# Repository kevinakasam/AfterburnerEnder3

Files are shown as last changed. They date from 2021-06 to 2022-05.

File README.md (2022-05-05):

## Afterburner Ender3 + Cable Chain + BL-Touch or PINDA + Raspberry Pi TFT

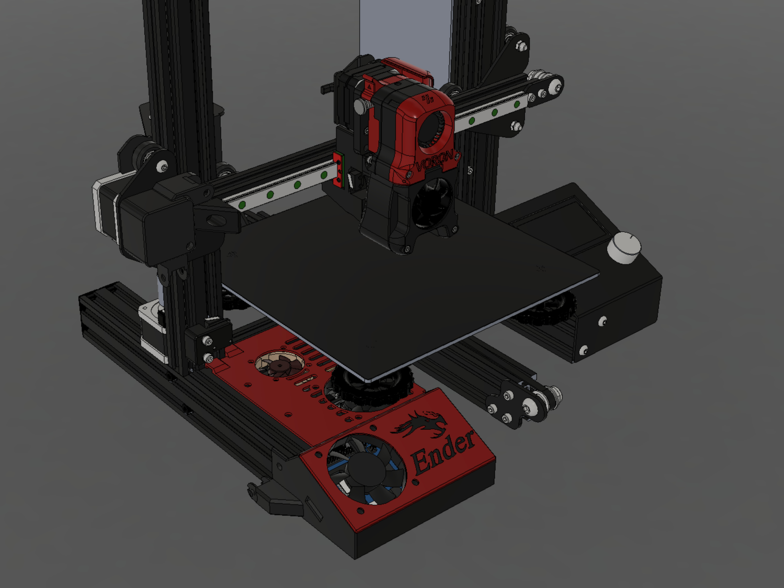
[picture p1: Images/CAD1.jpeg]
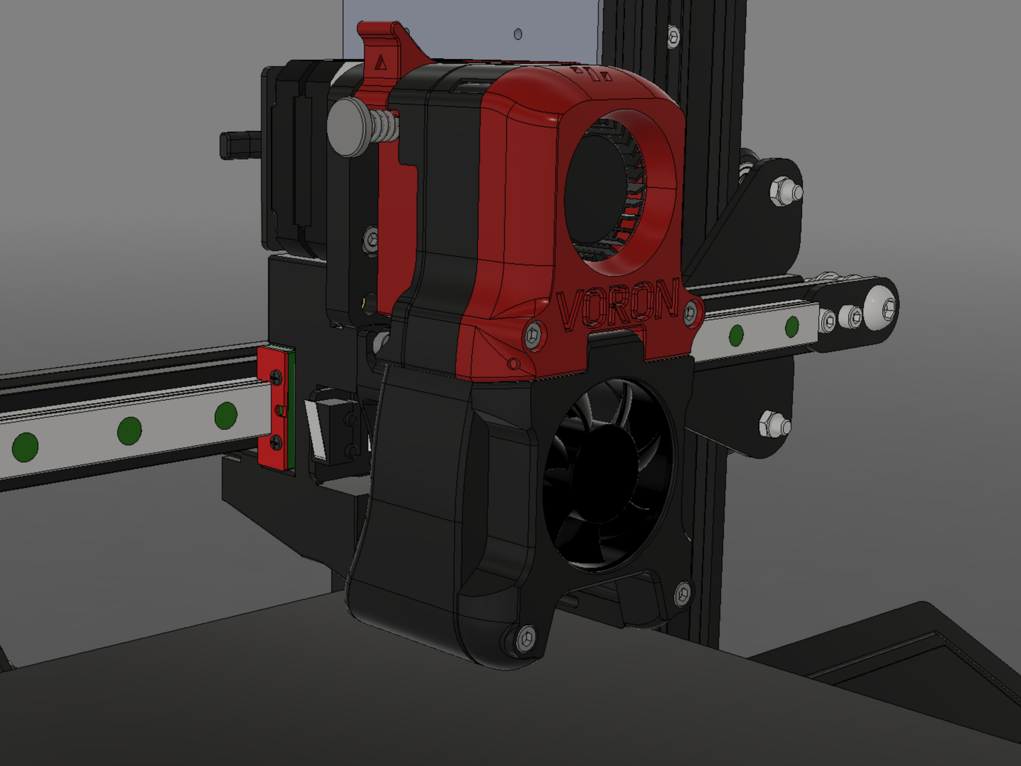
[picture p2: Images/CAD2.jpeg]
 
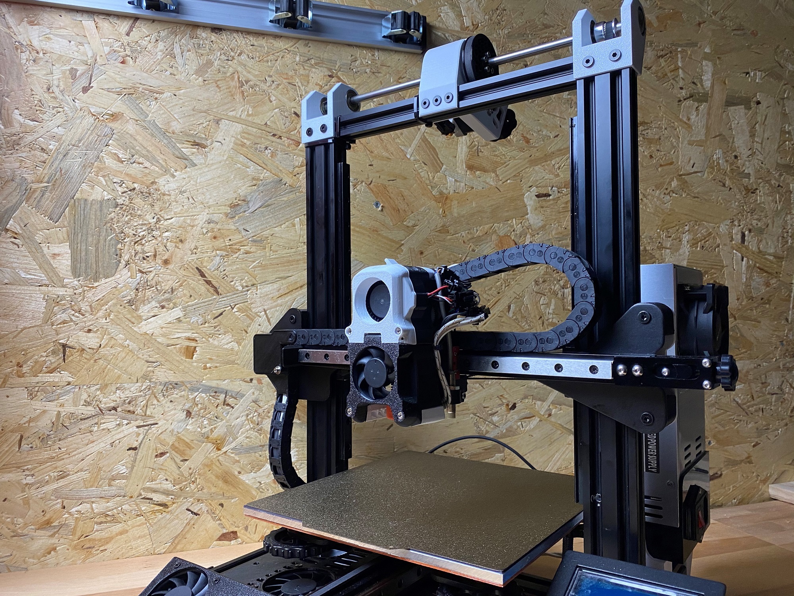
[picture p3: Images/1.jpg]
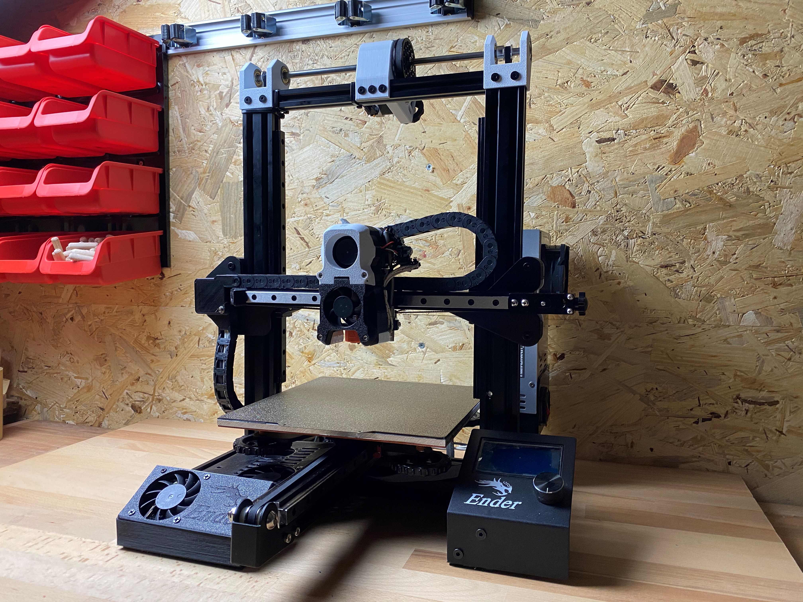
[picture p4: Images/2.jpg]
 

If you have any questions feel free to join the [Discord-Server](https://discord.gg/xqpKrxt9FC) 
 
<a href="https://discord.gg/xqpKrxt9FC">
         <img alt="Join" src="https://github.com/kevinakasam/BeltDrivenEnder3/blob/main/Pictures/Discord-Logo%2BWordmark-Color.png"
         width=250" >
      </a>

## Still in Progess
This page is currently only used to provide the files and basic instructions. More info and parts for the electronics, Raspi, BL-Touch etc will be added later.  

### Versions
1: PINDA or BL-Touch        |  2: Fan or Raspberry Pi TFT
:-------------------------:|:-------------------------:
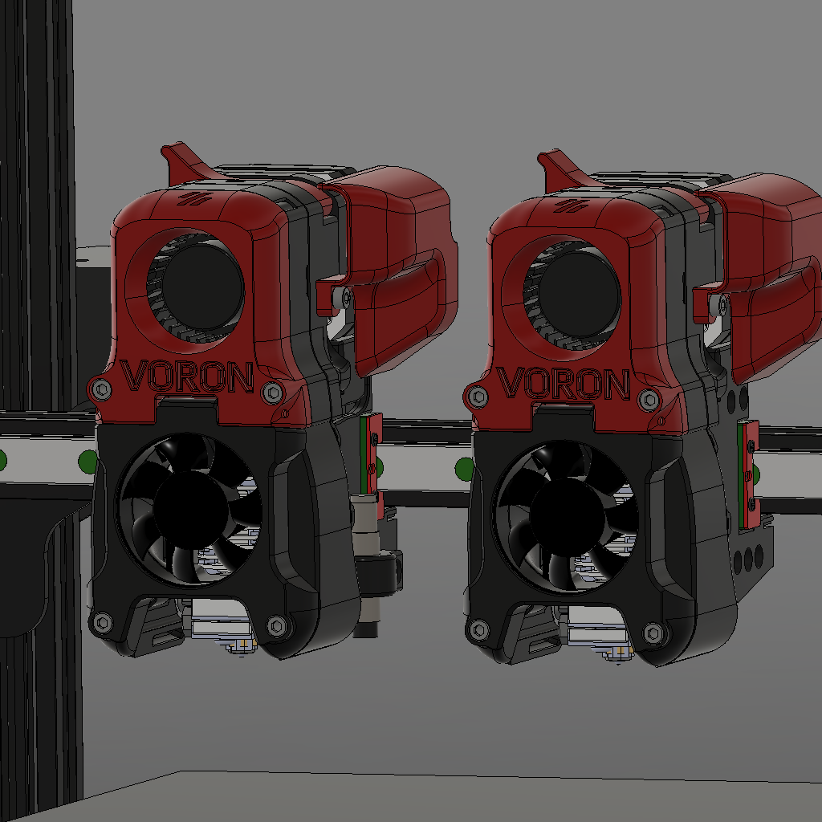
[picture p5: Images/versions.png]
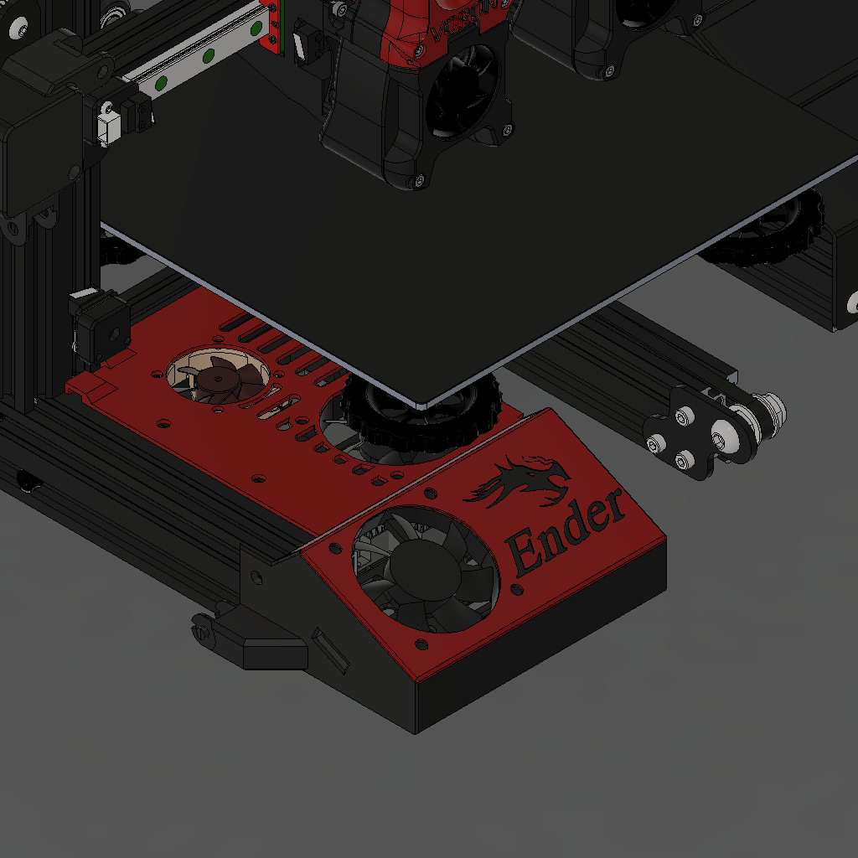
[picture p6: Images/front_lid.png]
  |  
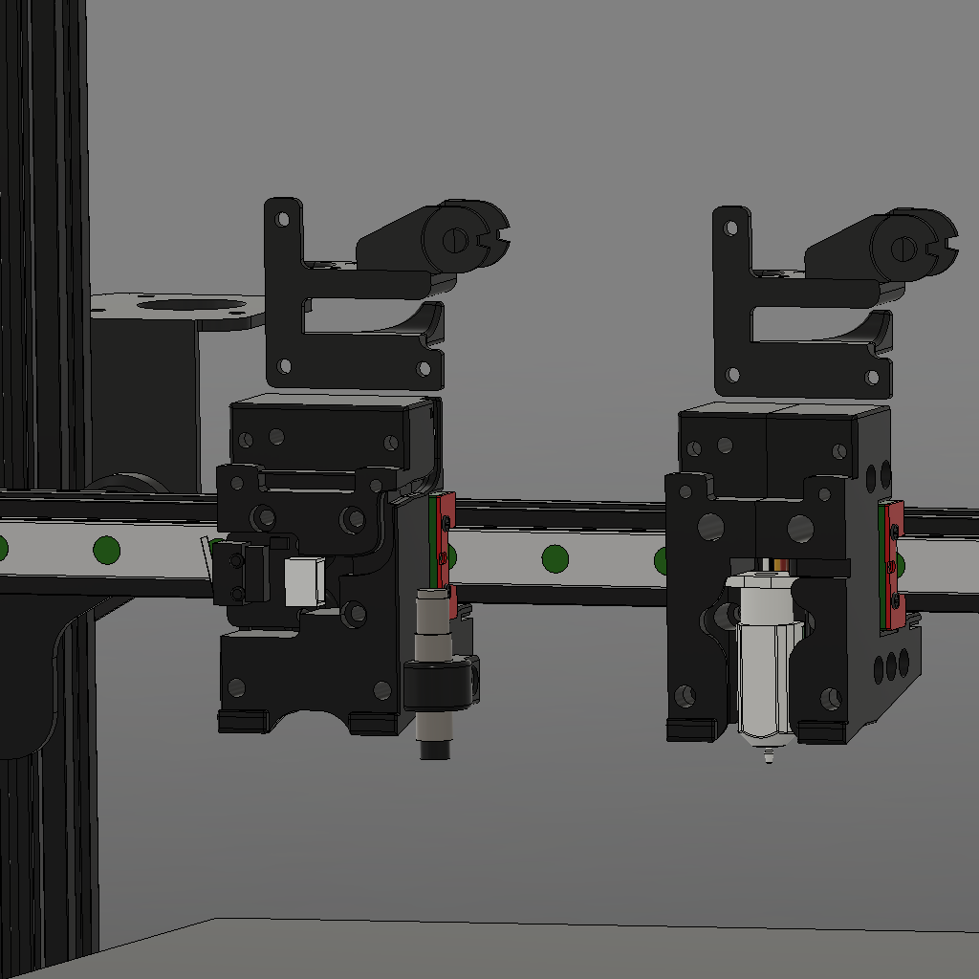
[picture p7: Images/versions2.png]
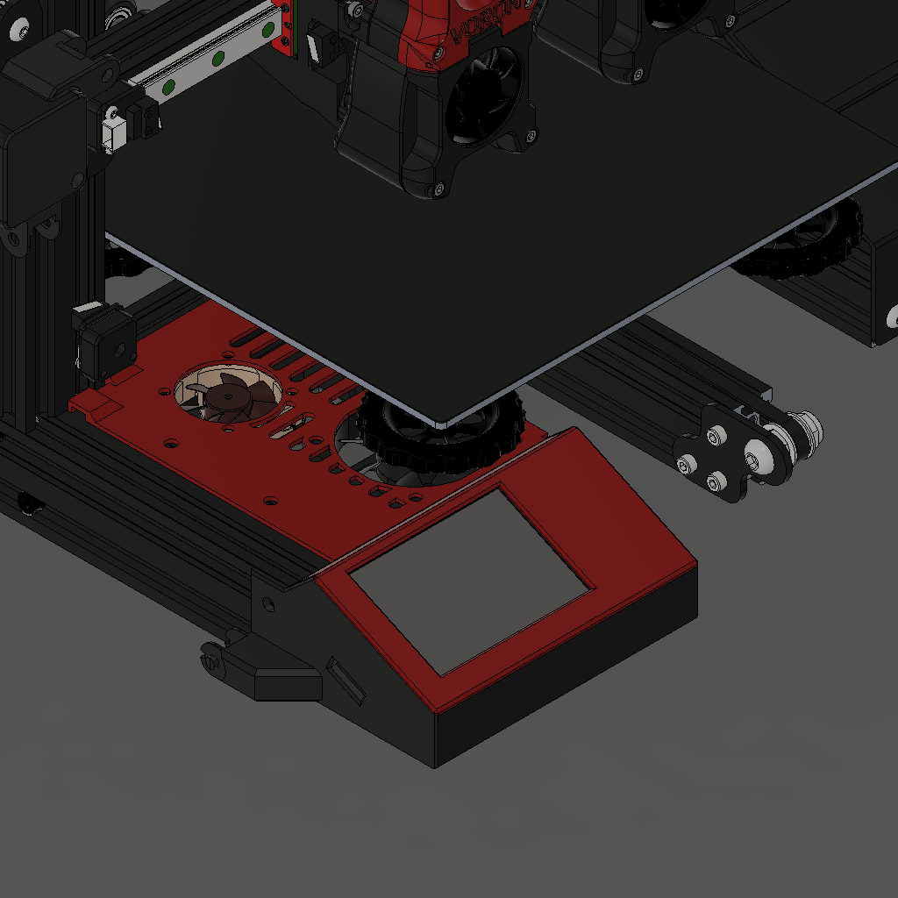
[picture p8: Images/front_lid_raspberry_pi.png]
  |  

### Why?
As you can probably guess, I love the Voron design. It makes me so much fun to work with the ideas and great designs that the team around Voron has created. And since the Afterburner not only looks nice but is also quite cheap and reliable, I decided to mount it on the Ender 3. This mod fits all Ender3 and similar machines like CR10 etc. Since the extruder had to come very far forward to be able to install the cable chain, I had a lot of space in the afterburner carriage. Therefore, I decided to integrate the limit switch into the carriage.

### A good Idea?
Definitely yes, if you can print with ABS(+). I first printed the parts out of PETG and I had a lot of problems. Besides that, the extruder is very strong like the normal BMG extruder and just works perfectly. I have been using the extruder continuously for weeks now and I am very happy with it.
If you are from Germany or the EU, please send me a message via Discord and I can print the parts for you.

### Important SAFTY notes
Do not use the original cables in the cable chain! Do not use PVC cables, these will break after some time! I replaced all my cables with silicone cables, so they do not break. You can also use PTFE cables or HELUKABEL, but this is much more expensive. If you are from Germany you can find cheap silicone cables in the online store from Conrad Electronik.

### How to print?
All parts can be printed without support (except x_motor_housing.stl; see STL Folder) and are already in the optimal orientation for printing. All Afterburner parts should be printed out of Abs. I'm using Esun ABS+, this is very easy tp print. But remember that the fumes are toxic, so use an enclosure and an air filter ([BFACH](https://github.com/kevinakasam/BFACH "BFACH")).

### BOM
* #### Rail
  * 1x MGN 12H 300mm
  * 12x M3x8mm (to mount the rail)
  * 12x M3 t-nut (to mount the rail)
  * 1x M5x8mm (to mount the limit block)
  * 1x M5 t-nut (to mount the limit block)
  * 2 Meter GT2 Belt (Glas Fiber reinforced)
* #### Afterburner Carriage Pinda
  * 3x M3x20mm
  * 1x M3x5mm
* #### Afterburner Carriage BL-Touch
  * 3x M3x20mm
  * 1x M3x5mm
  * 5x M3 brass heat insert
  * 5x M3x35mm
* #### PINDA Mout
  * 1x M3 brass heat insert
  * 1x M3x8mm
* #### BL-Touch Mount
  * 2x M3 brass heat insert
  * 2x M3x8mm
* #### Cable Chain
  * 1 Meter 10x11 cable chain (open and closed ine works. I used the open one for better access)
  * 3x M3 brass heat insert (for mounting to the chain anchor)
  * 3x M3x5mm (for mounting to the chain anchor)
* #### X Motor Housing
  * 3x M3x5mm (to mount the x-motor)
  * 1x M3x30mm (to mount the housing)
* #### Afterburner
  * Please use Voron sourcung guide: https://vorondesign.com/sourcing_guide (Click on the Afterburner sheet at the bottom)
  * **I'm using a 23mm nema. If you want to use a 20mm one you have to modify the parts!**
* #### Afterburner 5015 Mod
  * Please check Gregs page: https://github.com/Greg191134/Voron/tree/master/Afterburner%20Optimisation

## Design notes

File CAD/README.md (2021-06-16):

Feel free to edit the parts;)

 

Ender 3 CAD: https://github.com/Creality3DPrinting/Ender-3/tree/master/Ender-3%20Mechanical/F360

Afterburner CAD: https://github.com/VoronDesign/Voron-Afterburner/tree/master/CAD

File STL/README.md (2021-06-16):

### How to print?
All parts can be printed without support (except x_motor_housing.stl; see below) and are already in the optimal orientation for printing. All Afterburner parts should be printed out of Abs(+). I'm using Esun ABS(+), this is very easy tp print. But remember that the fumes are toxic, so use an enclosure and an air filter (spoiler: I'm going to release a very powerful fan soon). I added a small support structure to the afterburner_carraige.stl. just break it after printing (see red surface below).

I'm using Gregs Modulaar Fan Duct and 5015 Mod (https://github.com/Greg191134/Voron/tree/master/Afterburner%20Optimisation). I had a small gap between the extruder and tool part, so I moved the mounting holes 1mm up (see afterburner_carriage_5015mod.stl). Since I never tested the stock Afterburner, I don't know if this "error" also occurs with the normal Afterburner or only with Greg's mod. Feel free to give me feedback.

1: Add support to the upper chain mount        |  2: break the small bridge (red surface)
:-------------------------:|:-------------------------:
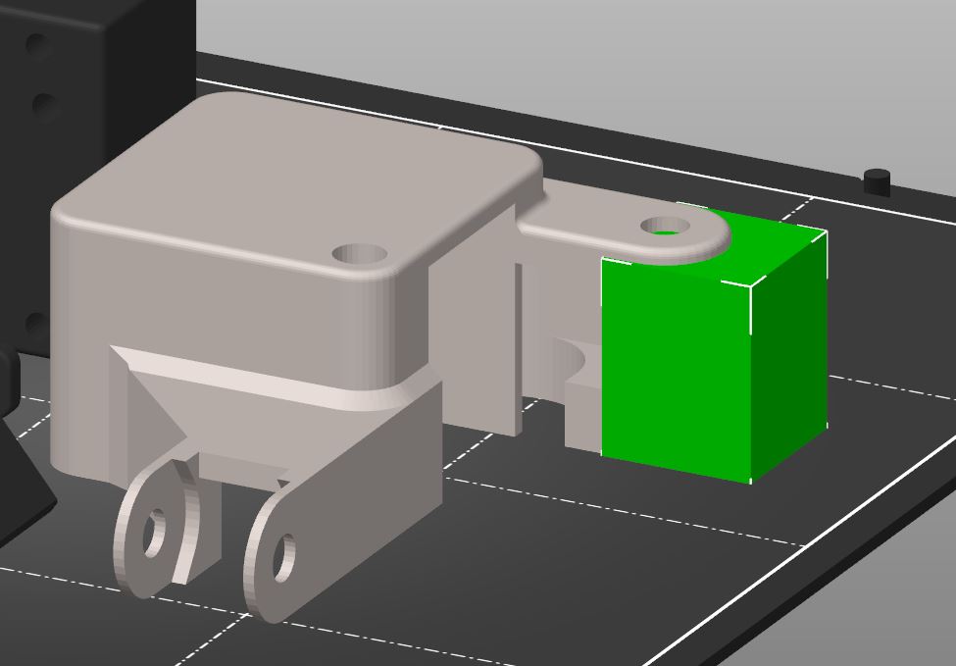
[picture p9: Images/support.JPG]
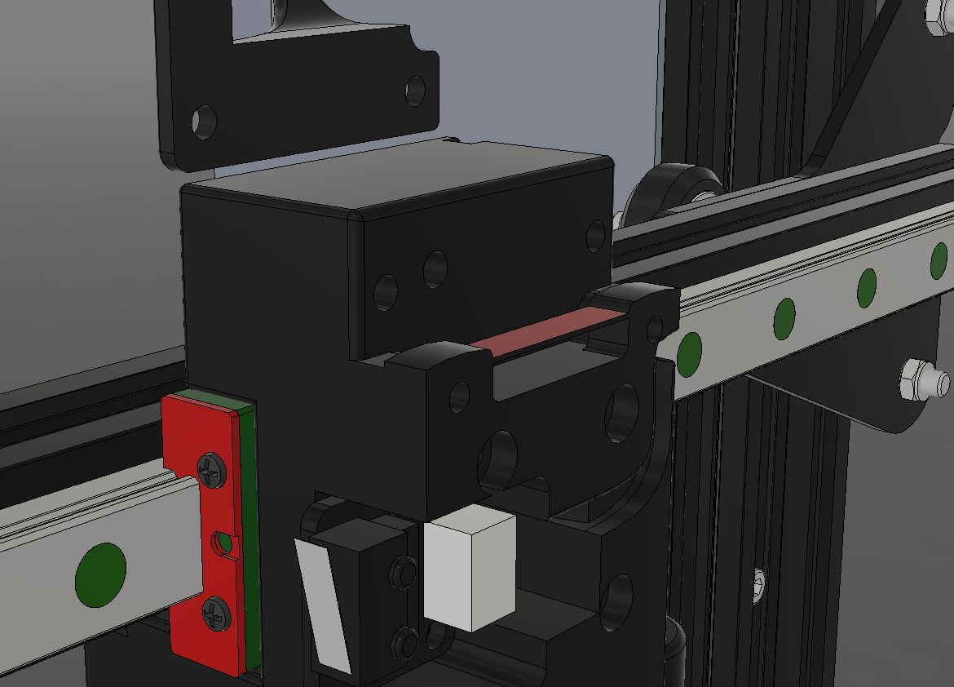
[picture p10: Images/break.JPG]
  |

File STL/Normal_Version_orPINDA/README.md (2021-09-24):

Carriage to mount the Afterburner to your Ender 3. Option to integrate the limit switch and add a PINDA. If you want to use a BL-Touch check the other version.

### How to print?
All parts can be printed without support and are already in the optimal orientation for printing.
I added a small support structure to the afterburner_carraige.stl (see red surface below). There's also some support in the end of the belt clamp. Just break both after printing.

I'm using Gregs Modulaar Fan Duct and 5015 Mod (https://github.com/Greg191134/Voron/tree/master/Afterburner%20Optimisation). I had a small gap between the extruder and tool part, so I moved the mounting holes 1mm up (see afterburner_carriage_5015mod.stl). Since I never tested the stock Afterburner, I don't know if this "error" also occurs with the normal Afterburner or only with Greg's mod. Feel free to give me feedback.



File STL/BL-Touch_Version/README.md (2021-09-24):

Mount that integrates the BL-Touch like the original Omron TL-Q5MC2. Very clean solution. All credits go to Guffy who came up with the idea and finished the design!

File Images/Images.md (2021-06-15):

Images.

Also check:

Video Tutorial (https://www.youtube.com/watch?v=bxTwFCPEIgg&t=1s)

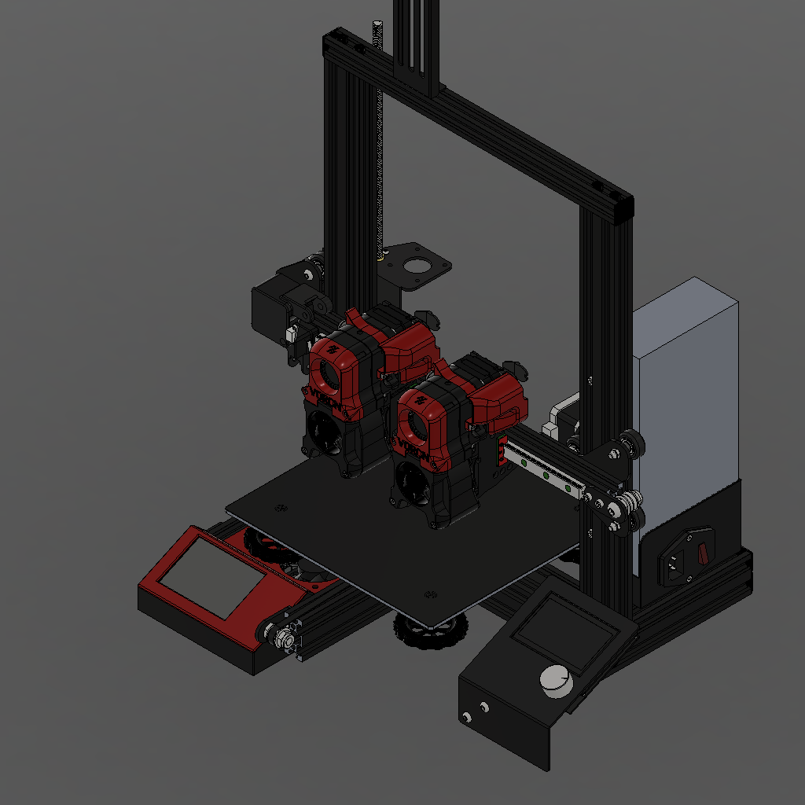
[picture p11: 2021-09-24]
Images/Ender3-AB.png

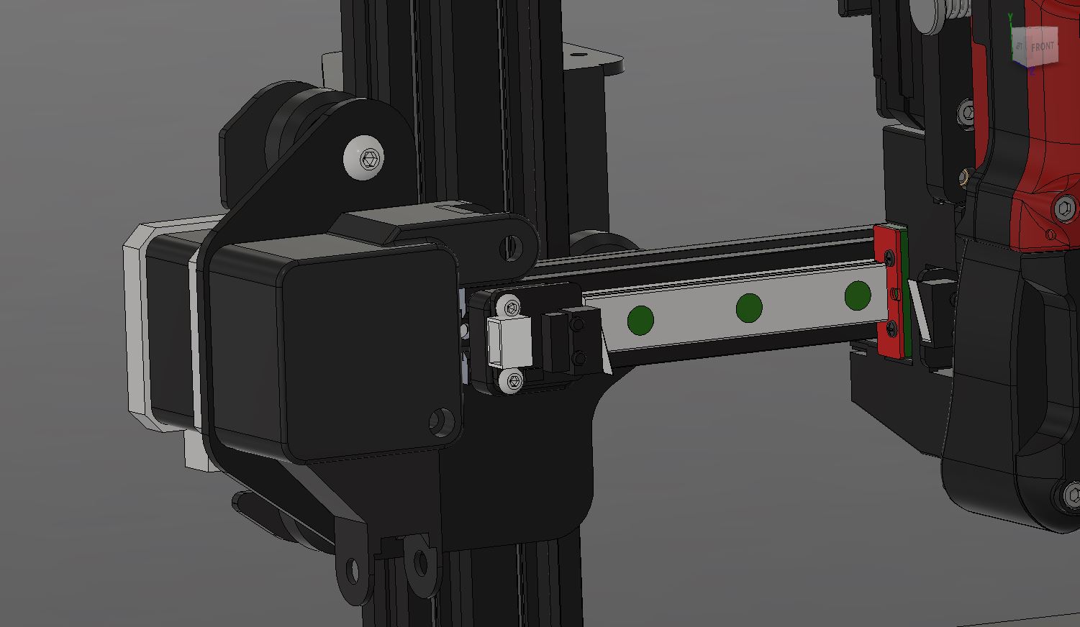
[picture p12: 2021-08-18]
Images/untested.JPG

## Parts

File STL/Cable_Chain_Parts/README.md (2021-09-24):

These parts are common to both versions(BL-Touch and normal). You need these parts to mount the chain.

### How to print?
All parts can be printed without support (except x_motor_housing.stl; see below) and are already in the optimal orientation for printing. 

### Add support to the upper chain mount


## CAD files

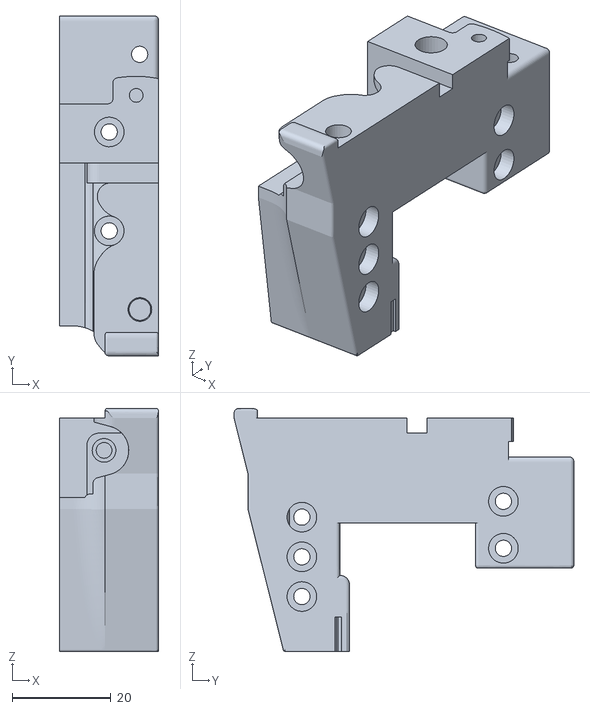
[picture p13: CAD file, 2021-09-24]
STL/BL-Touch_Version/BLT_Carriage_B.stl
20.0 x 68.8 x 49.2

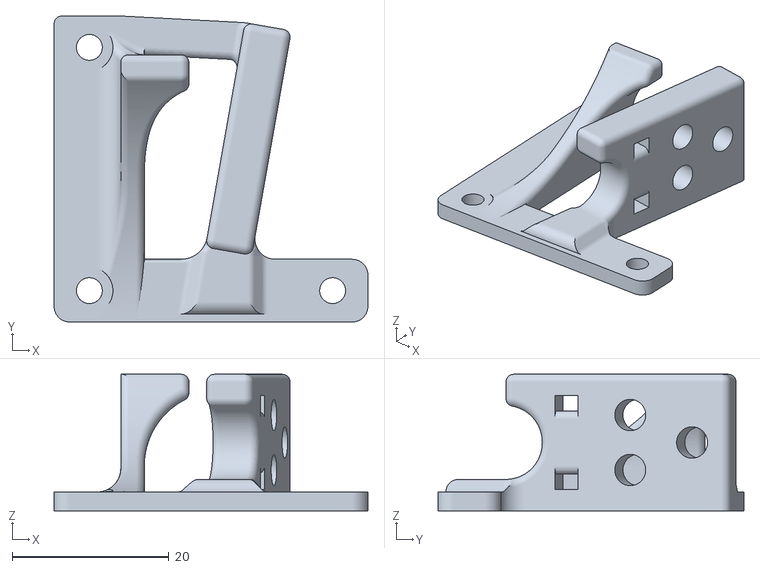
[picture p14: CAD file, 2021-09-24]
STL/Cable_Chain_Parts/chain_anchor_nema23_angled.stl
40.0 x 39.0 x 17.4

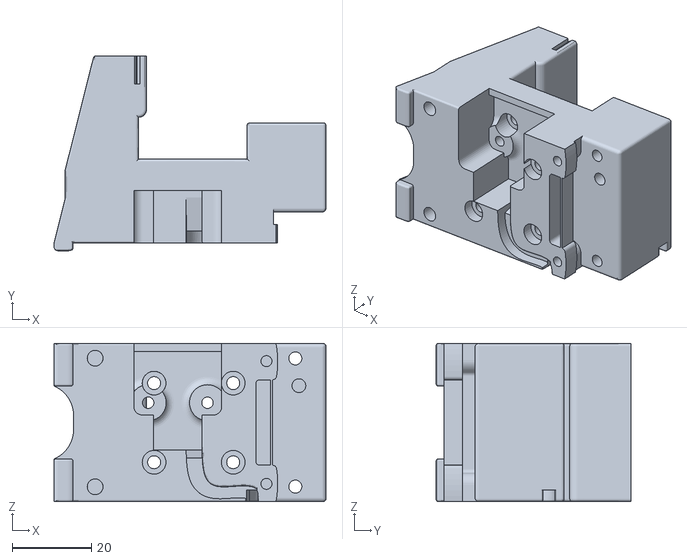
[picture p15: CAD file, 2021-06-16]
STL/Normal_Version_orPINDA/afterburner_carriage_5015mod.stl
68.8 x 49.2 x 40.0

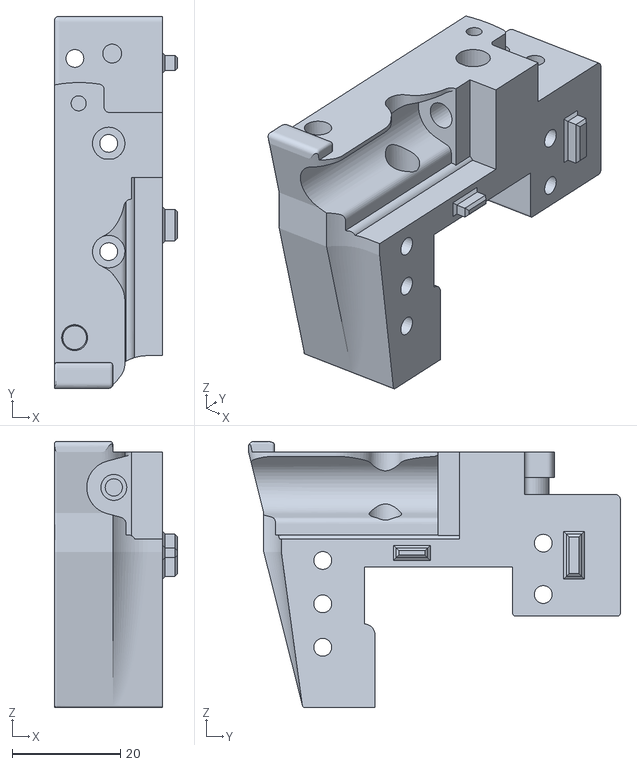
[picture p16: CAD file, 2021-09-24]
STL/BL-Touch_Version/BLT_Carriage_A.stl
22.8 x 68.8 x 49.2

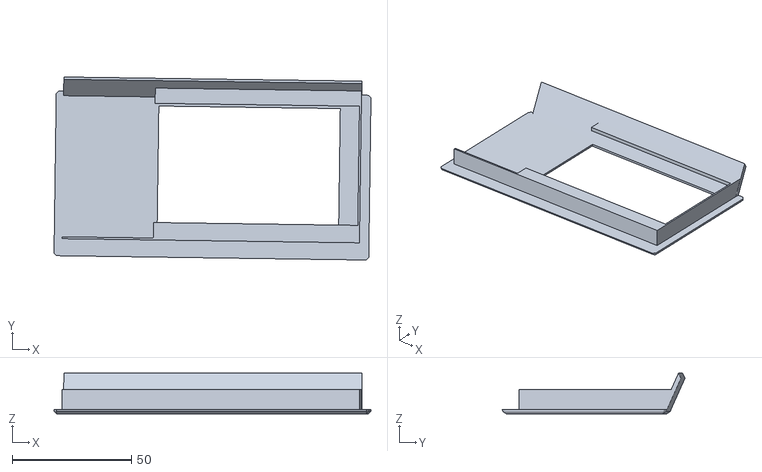
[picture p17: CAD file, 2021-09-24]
STL/Cable_Chain_Parts/front_lid_raspberry_display_holder.stl
133.1 x 76.9 x 17.1

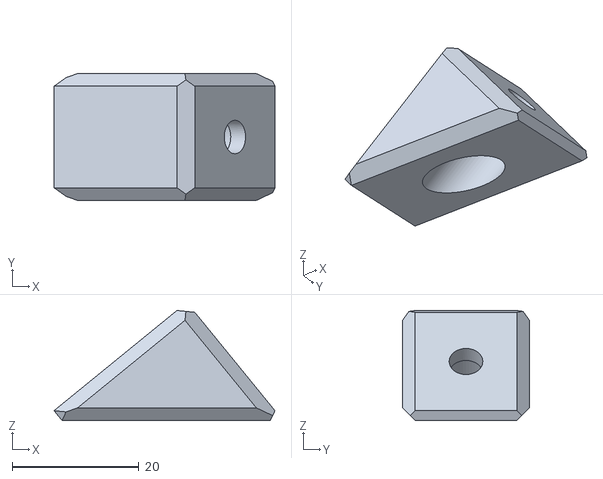
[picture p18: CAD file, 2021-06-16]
STL/Normal_Version_orPINDA/limit_block.stl
34.8 x 20.0 x 17.3

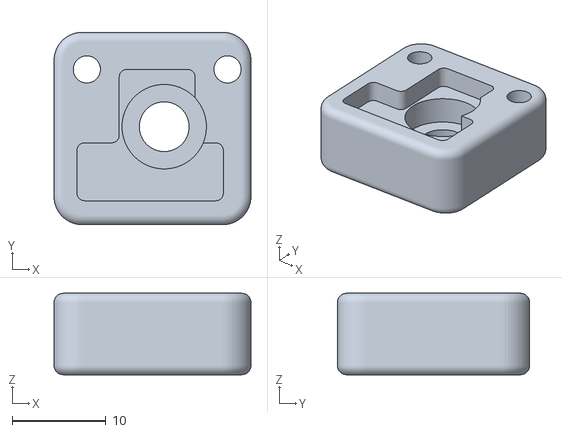
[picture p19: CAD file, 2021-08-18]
STL/BL-Touch_Version/X_limit_switch.stl
21.0 x 20.5 x 8.70

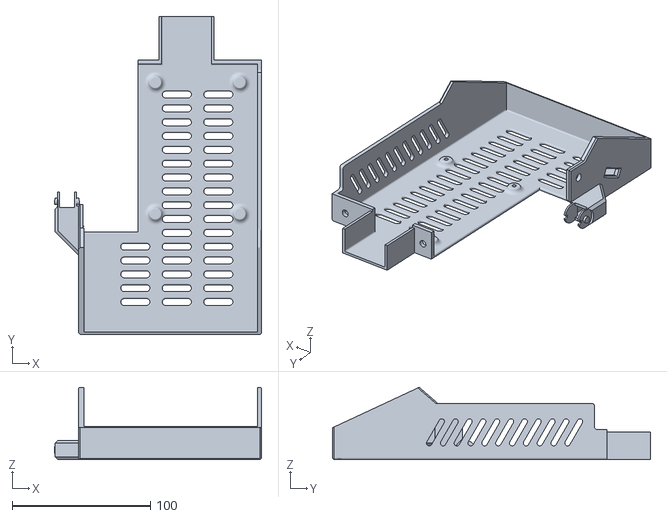
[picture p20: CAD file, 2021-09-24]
STL/Cable_Chain_Parts/electronic_box_einsy.stl
149.7 x 230.0 x 52.4

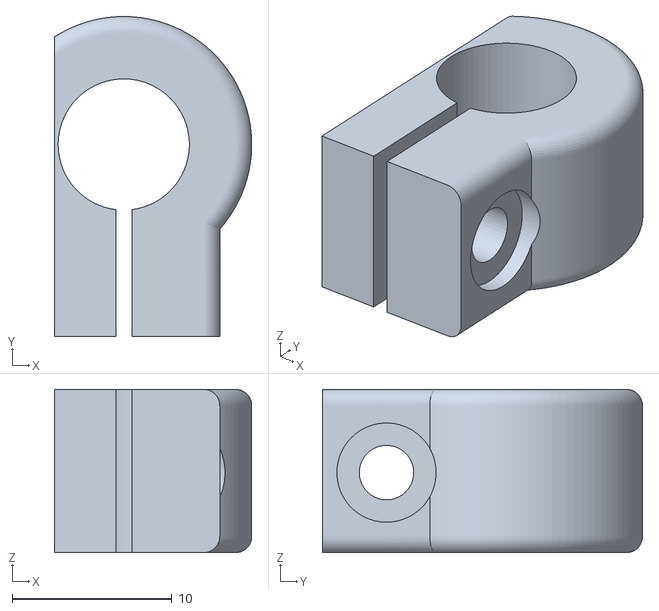
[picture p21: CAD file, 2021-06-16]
STL/Normal_Version_orPINDA/pinda_holder.stl
12.3 x 20.0 x 10.2

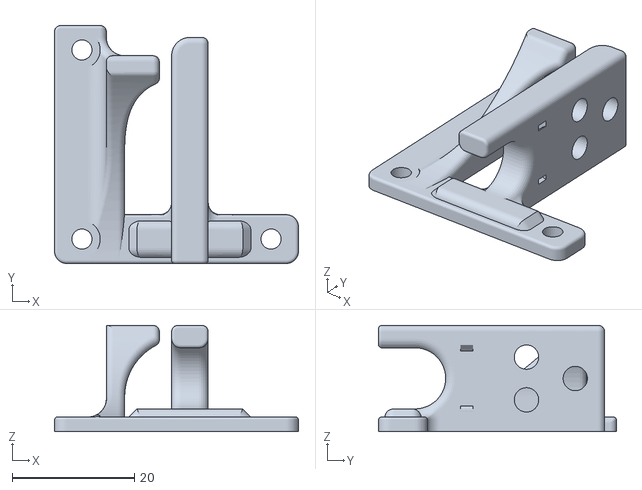
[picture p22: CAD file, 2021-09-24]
STL/Cable_Chain_Parts/chain_anchor_23mm_nema.stl
40.0 x 39.0 x 17.4

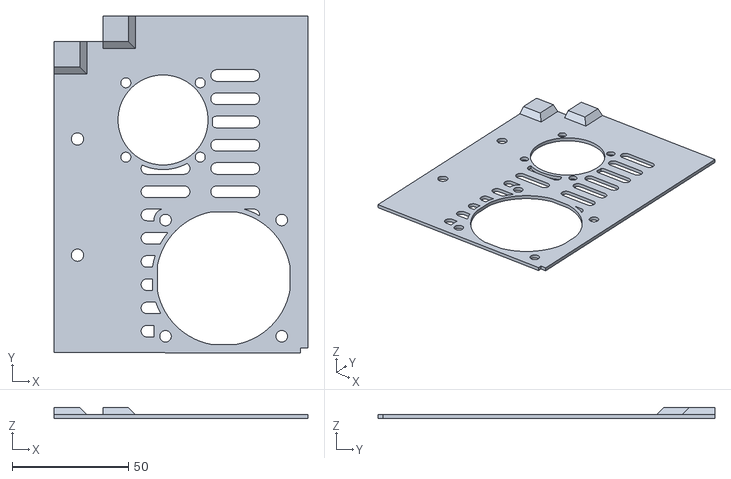
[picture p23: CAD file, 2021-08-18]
STL/Cable_Chain_Parts/top_lid.stl
109.1 x 145.0 x 4.81

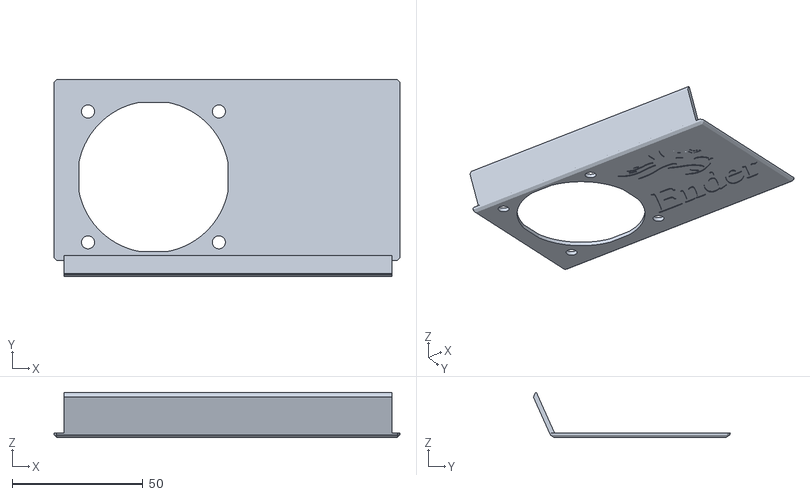
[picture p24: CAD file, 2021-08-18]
STL/Cable_Chain_Parts/front_lid.stl
132.2 x 75.4 x 17.3

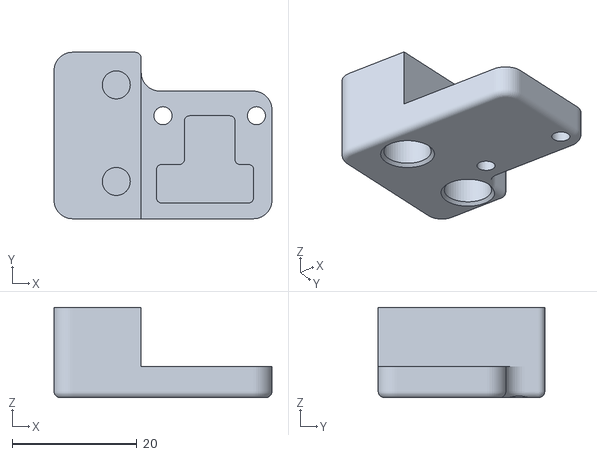
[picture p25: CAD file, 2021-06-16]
STL/Cable_Chain_Parts/limit_switch.stl
35.0 x 26.8 x 14.5

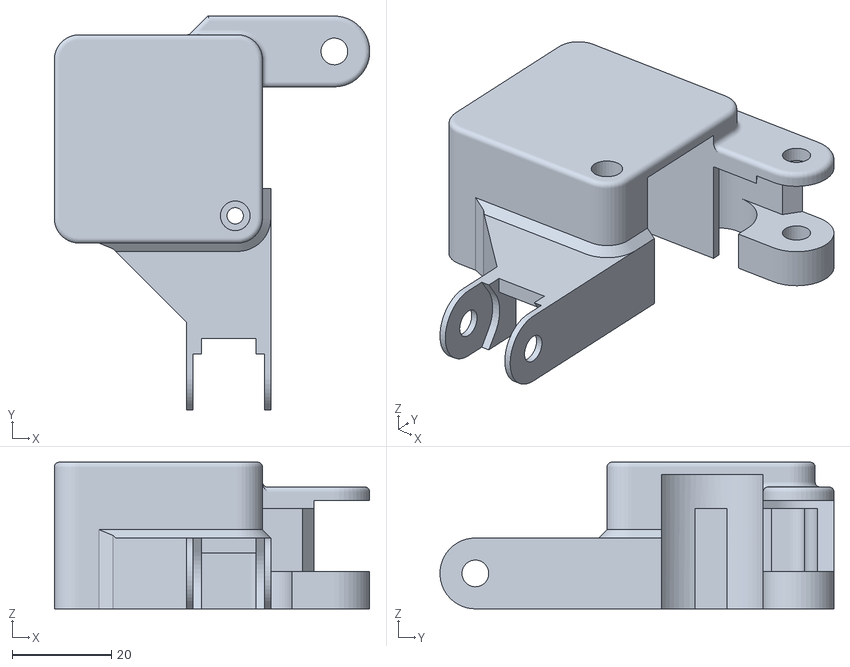
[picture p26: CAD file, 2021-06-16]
STL/Cable_Chain_Parts/x_motor_housing.stl
63.6 x 79.5 x 29.6

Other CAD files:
STL/Normal_Version_orPINDA/afterburner_carriage.stl
STL/Cable_Chain_Parts/electronic_box_stock_skr_mini.stl

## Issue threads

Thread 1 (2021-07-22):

Add x endstop to original place

zx4017555, 2021-07-22:
Hi, I saw how cleverlu you designed the belt mod, so I decided to look at what else you designed, and found this, turns out, I also have an afterburner installed already, and I love the positioning of the cable chain, but I don't want to reposition the endstop on the duct, one more wire to the duct, one more point of failure etc, and I tend to swap ducts for comparison, ik this is a wip, but can you consider adding the x endstop into the housing like the stock one, thanks!

kevinakasam, 2021-07-22:
Hey, thanks:) Because of the cable chain I had to move the hotend a lot, so there was a lot of unused space. Thats why I moved the endstop inside the carriage because there is a lot of space. But I understand what you mean, I can make a new housing that has space for the endstop. You should be able to swap ducts as easy as usual, even with the endstop integrated. I will upload a step later;)

zx4017555, 2021-07-22:
Thank you! Love your work.

mihneaCR, 2021-08-08:
Hi, any progress on this? would also be very interested, unfortunately my CAD skills are not up to par yet to be able to do this mod myself.

kevinakasam, 2021-08-10:
> Hi, any progress on this? would also be very interested, unfortunately my CAD skills are not up to par yet to be able to do this mod myself.

Hey. Yes it's still in progress. I'm working on the bl touch version rn. I will make this at the Same time;)

mihneaCR, 2021-08-13:
> > Hi, any progress on this? would also be very interested, unfortunately my CAD skills are not up to par yet to be able to do this mod myself.
>
> Hey. Yes it's still in progress. I'm working on the bl touch version rn. I will make this at the Same time;)

Thanks, will keep an eye on it!

kevinakasam, 2021-08-18:
@mihneaCR @zx4017555
I added a file to mount the switch, not my best idea, but I couldnt find a clean solution.
[Image](https://github.com/kevinakasam/AfterburnerEnder3/blob/main/Images/untested.JPG)

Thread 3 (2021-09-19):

Length of linear rails in BOM?

Dingushippo, 2021-09-19:
Would be nice to know specifically what length is required

:)

kevinakasam, 2021-09-20:
Hey sorry for my late response. I used a 300mm rail :)

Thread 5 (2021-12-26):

nema 17 23mm does not fit when installed on the extruder body

madorax251, 2021-12-26:
i printed afterburner ender 3 mod. i use nema 17 23mm as you wrote on GitHub page but when i install extruder body clockwork shaft stepper motor stuck on extruder body page. can you help me to solve this?

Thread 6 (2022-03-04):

belt clip is too narrow

madorax251, 2022-03-04:
i printed the afterburer carriage bltouch but having trouble attaching the belt. the clip on the carriage is too narrow

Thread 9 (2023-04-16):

split this project to two - afterburner and other "rpi case" ?

Hrumque, 2023-04-16:
The housing for electronics is not well documented - we do not know which rpi display fits into this housing, how to mount it, how to mount the rpi in the housing, how to connect (with glue?) the top and front panel with the housing base...
Front housing for the display - requires supports in the print. It could be redone.
Maybe separate this project as a separate part, just like you could develop it yourself? CAD files of the case itself would be useful, because a lot could be improved in it.

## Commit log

2021-06-16 Added X Axis Parts
    [afterburner_carriage.stl, afterburner_carriage_5015mod.stl, chain_anchor_23mm_nema.stl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]
2021-06-16 Added Z Limit Switch
    [limit_switch.stl]
2021-06-16 Update and rename CAD.me to CAD.md
2021-06-16 Added CAD File
2021-09-24 Made by Christian. Less stress on cables.
    [chain_anchor_nema23_angled.stl]
